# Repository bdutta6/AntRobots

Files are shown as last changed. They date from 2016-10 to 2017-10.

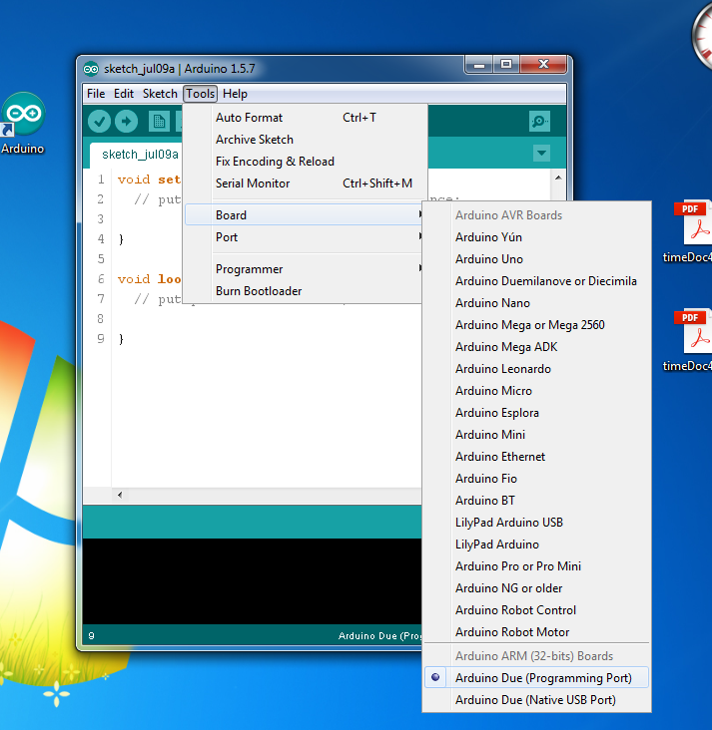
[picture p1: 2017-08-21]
docs/gettingStartedDoc/progPort.png

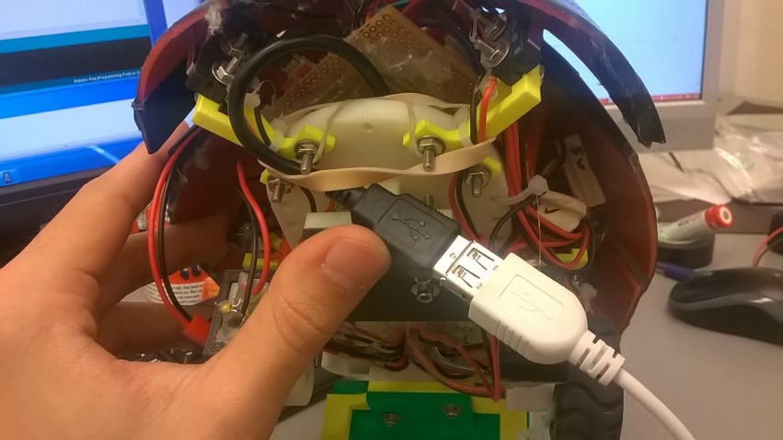
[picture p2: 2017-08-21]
docs/gettingStartedDoc/usbConnection.jpg

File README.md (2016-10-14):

# ant-robots

##Contributors

Initial Author: Vadim Linevich  
Email: vadim.linevich@gmail.com  

Modified by: Jungsoo Park  
Email : ryanryan0906@hotmail.com  

Modified by: Bahnisikha Dutta  
Email : bahnisikha3474@gmail.com  

Modified by: Ross Warkentin  
Email: ross.warkentin@gmail.com  

[Guide to .md files](https://guides.github.com/features/mastering-markdown/)

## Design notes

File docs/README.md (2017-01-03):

### September 27, 2016 
This serves as an e-introduction among all of us—Magnus and I are interested to see if his swarm work can be integrated with our ant robot work to learn if collisions among densely packed task oriented collectives of robots can be used to ensure good flow, etc. I suggest that all the students and postdocs cc’d on this email self-organize to trade info on what we (they) are doing and then in the coming weeks we can all meet to see if anything emerges...The new research direction on using ant-inspired collisions in swarm robot control/localization seems very interesting.

### October 4, 2016  
Grad Groups meeting today featured a woman from the library who overviewed the different resources available to graduate students. For research in engineering, she recommended compendex and inspec as good databases.

### October 5, 2016
I was supposed to have a Skype call with JSP today to review the robotic ant systems, but he was not able to get online. Instead, we chatted on the phone, and I took down the following notes:

* Mechanically it is sort of sorted out
  *	Two of them are not working well (Echo and Charlie?)
* When you connect the batteries, you need to separate the batteries completely off of the wires
* Issues are not commented within the code

I also spent a good amount of time today studying the codebase and learning its architecture. I think I have a good understanding of it, and I love the thorough documentation. I am not sure I understand the Watch Dog Timers (WTD), and I haven’t found a satisfactory explanation of them online. I would love an explanation of them from JSP.

### October 6, 2016  
I continued reviewing the code, and Dr. Goldman showed me how to turn on the robots. There is a black switch on the side which turns it on and off, as well as a button on the main board which can be used to reset the robot.
All of the batteries were dead, so there are two things that I need to do to get started:

1. Learn how to charge the batteries
2. Make a power cable so that the robots can run off of a power supply (3.6V).

### October 7, 2016

Will mentioned to me yesterday that the recharging process while the ants are running is not a straightforward process, and there are several files floating around on the lab desktop with tables I think might be necessary for regulating the charging method. See “C:\Users\vlinevich3\Desktop\Charging MPR121 Program vals.xlsx”.

Continued going through the documentation left by JSP and fleshing out the Robotic Ant Status to get a better feel for the architecture and pre-existing problems. I also started up a Trello Board to track proposed changes from JSP. The Trello board is populated with the “List of things that need to be done in the future” in the Ant Robot Mk.2 Software Documentation

Calling it a day. Feeling better about navigating the code. There seems to be some extraneous stuff left over from previous iterations, but I’d prefer to just get things running for now before going back and modifying working code to basically just look pretty. Best practices can be implemented after I have proven that I can get data with what we have right now.

I was hoping to hear from JSP today, but I might just shoot him an email with all of my documented questions later tonight.

[Guide to .md files](https://guides.github.com/features/mastering-markdown/)

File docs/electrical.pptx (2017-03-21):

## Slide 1

Bat 3.7-4.2V

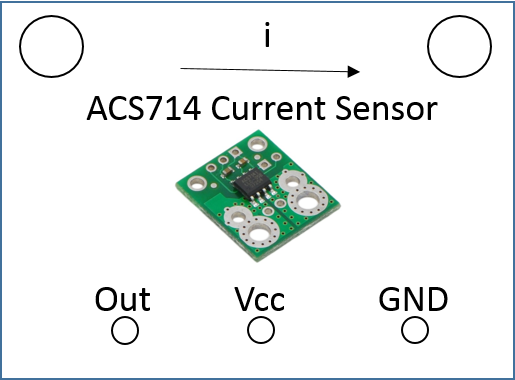
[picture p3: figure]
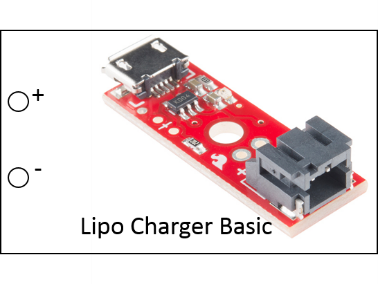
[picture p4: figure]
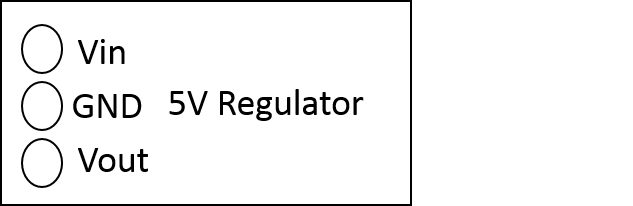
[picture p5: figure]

Due I/O Pin

Due Vin

Due 5V

Due Control Pin

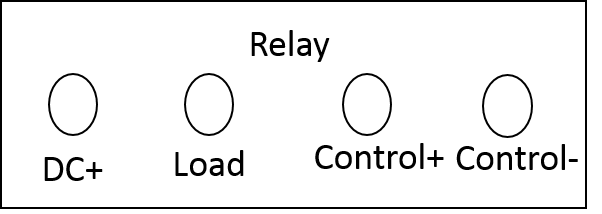
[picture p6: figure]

5V High current line

Batt GND

Due GND

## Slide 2

Vin

WW

GND

Vout

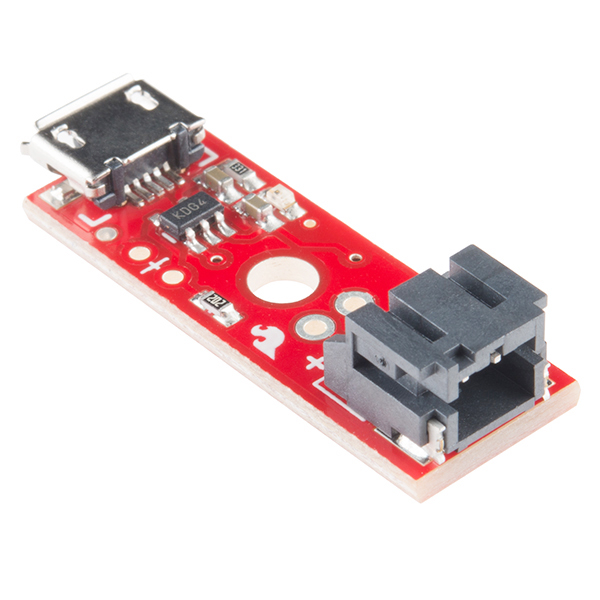
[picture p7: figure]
SparkFun LiPo Charger Basic - Micro-USB

Lipo Charger Basic

+

ACS714 Current Sensor

i

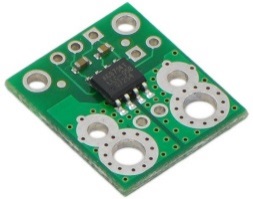
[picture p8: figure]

Out

Vcc

GND

Relay

DC+

Load

Control+

Control-

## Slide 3

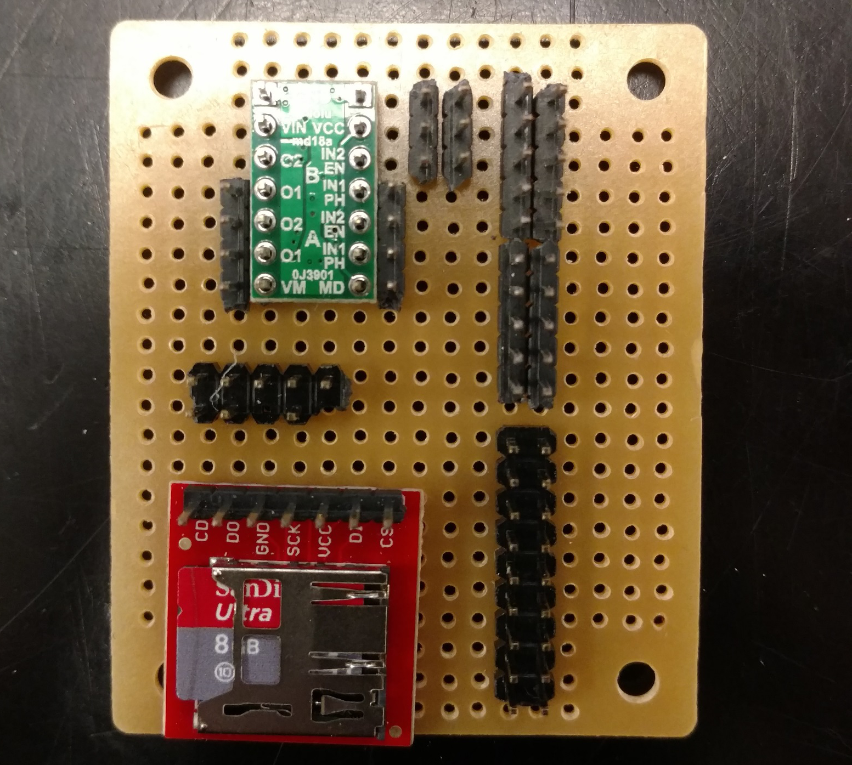
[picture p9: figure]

5V High Current

GND Due

GND

5V Due

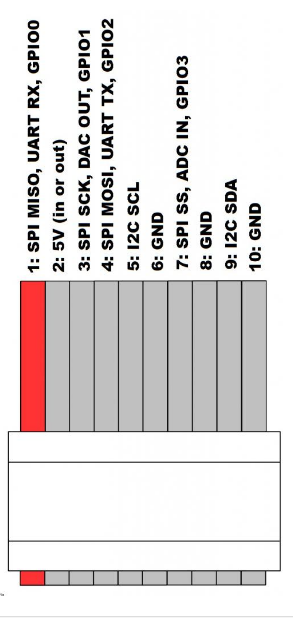
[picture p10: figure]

3.3V Due

Due Pin 4

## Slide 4

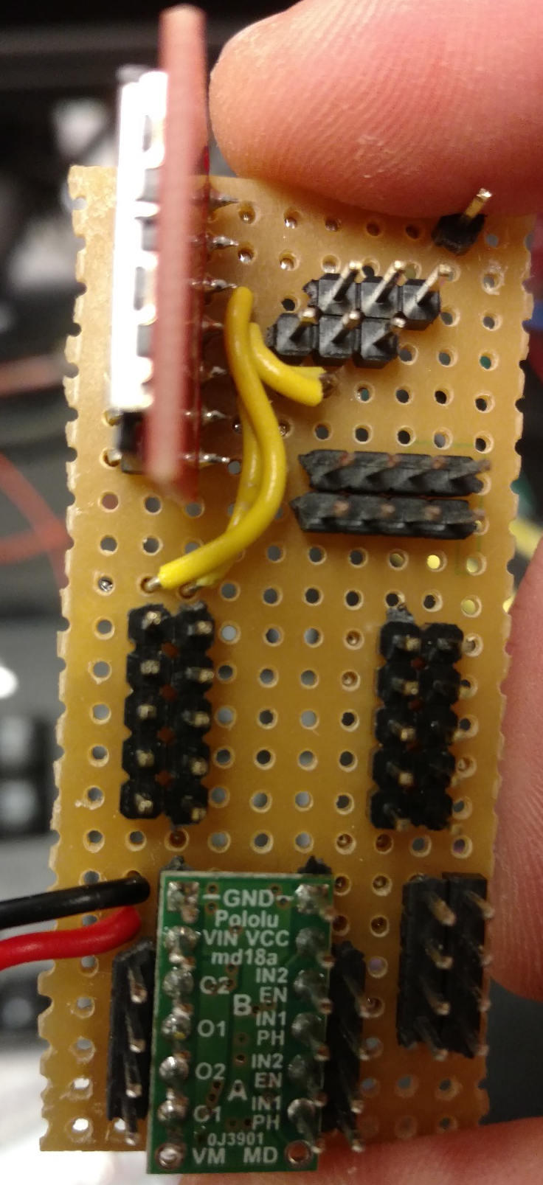
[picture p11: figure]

1 2
3 4
5 6
7 8
9 10

SPI Ribbon - Chip Reader:
1 – D0
3 – SCK
4 – D1

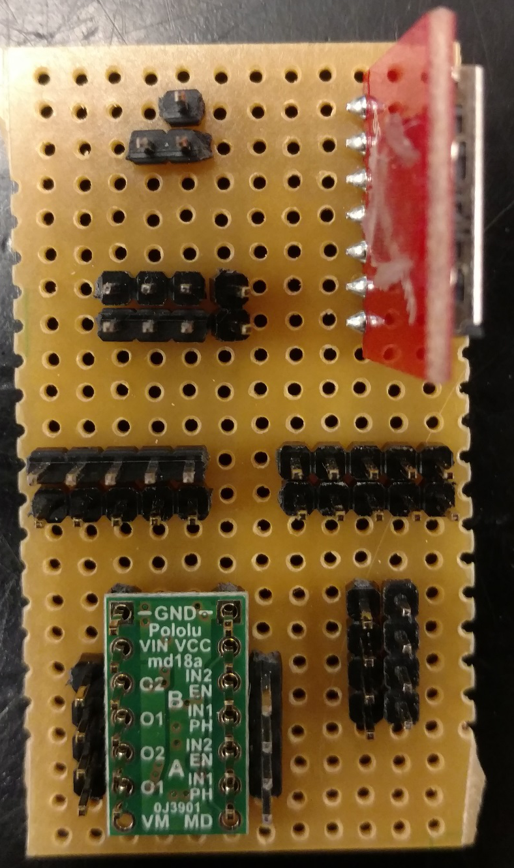
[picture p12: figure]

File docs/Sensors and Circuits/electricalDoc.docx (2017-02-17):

Due 5V – 800mA max

- Current sensor (draws 13mA at 5V)
- Hall effect sensors (9mA each x 4 sensors = 36mA total)
- Pixy (150mA at 5V)

Due 3.3V – 800 mA max

- Mag3110 is 0.9mA max with required voltage between 1.95 and 3.6V
- MPR121 is 29microA at 1.71 to 3.6V
- IMU is 350 microA

5V regulated power supply

- Gripper servo with 1.2A stall current
- Pitch servo with 1.2A stall current
- Motor board 1.25A stall current each = 2.5A total
- Due Vin

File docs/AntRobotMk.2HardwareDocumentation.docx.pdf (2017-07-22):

# Ant Robot Mk.2 Hardware Documentation

Jungsoo Park

CRAB Laboratory

Georgia Institute of Technology

626-720-3140

ryanryan0906@hotmail.com

Added Sensors/Systems

- Magnetometer: (https://www.sparkfun.com/products/12670)

The ant robot has one magnetometer sensor located in the front lower section of the robot, as shown in figure 1, to detect any magnetic cohesive material in the front. This sensor is used to inform when the robot has reached the digging site, and trigger the excavation behavior.

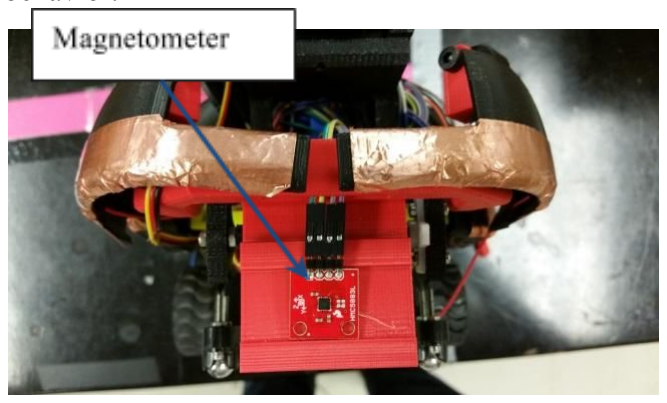
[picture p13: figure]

Figure 1: Magnetometer

- Gripper System:

The gripper system on the previous design featured a small gripper and servo, with an IR sensor to detect material in front, as shown in figure 2. In contrast, the new ant robot features more advanced gripper system, as shown in figure 3. It has much bigger gripper and stronger servo. In addition, it features more intelligent sensing capabilities, with the addition of Hall Effect sensors and force sensitive resistors. As a result, it is capable of excavating several times more material than that of the previous design. Furthermore, to ensure that the gripper system does not interfere with the robot’s capacitive sensors, it is designed to retract itself when it is not being used, but extend only when it is digging or depositing the material. Figure 3a shows the gripper in extended position, and figure 3b shows the gripper in retracted position. Figure 3c and figure 3d shows the griper in open position and closed position, respectively.

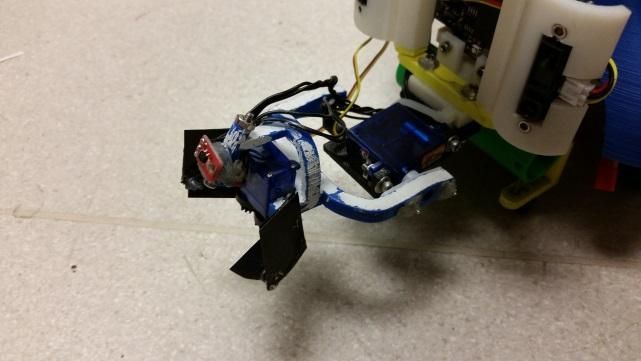
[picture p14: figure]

Figure 2: Gripper, Previous Design

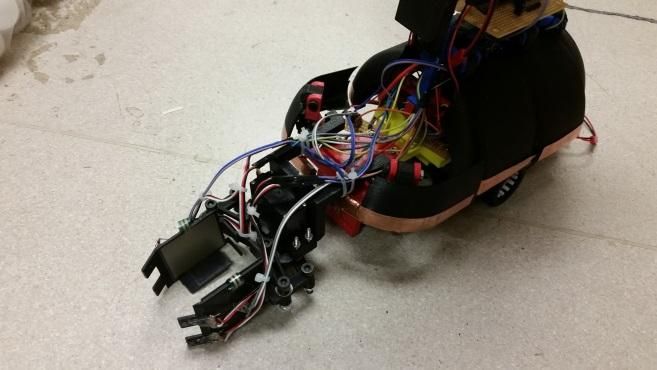
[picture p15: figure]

Figure 3a: Gripper, Extended Position

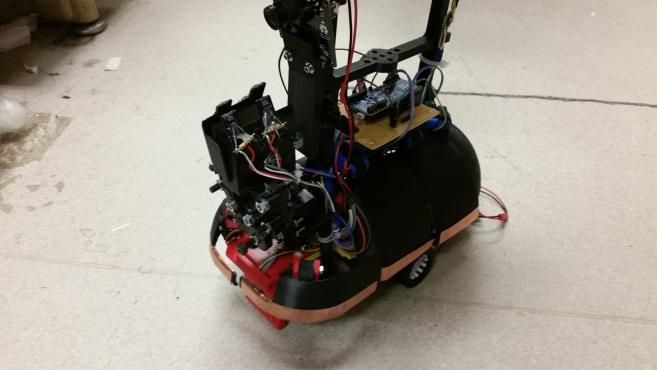
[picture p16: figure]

Figure 3b: Gripper, Retracted Position

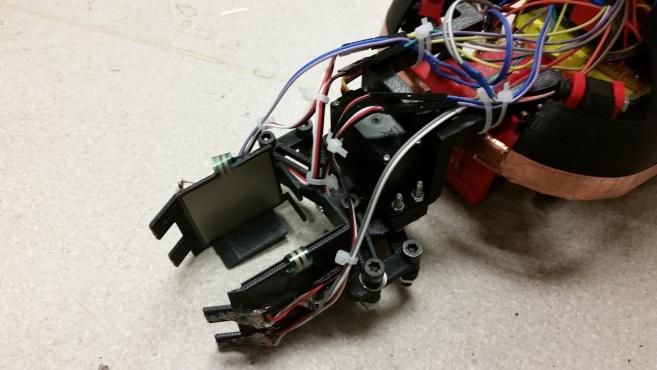
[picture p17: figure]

Figure 3c: Gripper, Open Position

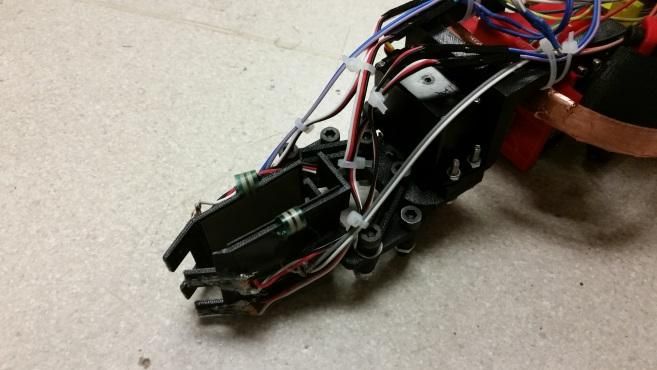
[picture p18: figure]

Figure 3d: Gripper, Closed Position

- Hall Effect Sensor:

Four Hall Effect sensors are located at the front tip of the gripper, as shown in figure 4. It is used as an alternative way to detect any magnetic cohesive material in front, as when the gripper is in extended position, it blocks the magnetometer and prevents it from detecting the magnetic cohesive material. In addition, these Hall Effect sensors can detect the accurate position of magnetic cohesive materials. This enables the robot to accurately position the gripper for optimal digging.

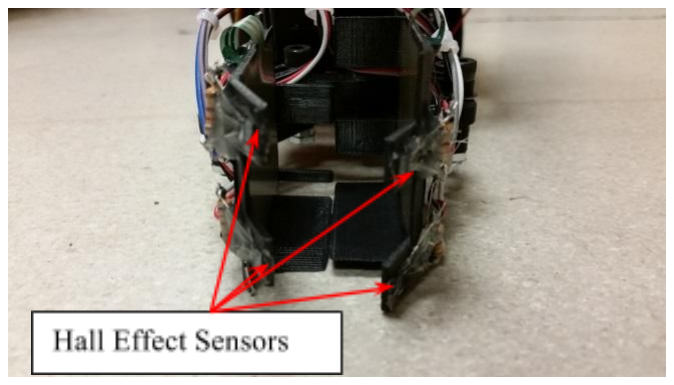
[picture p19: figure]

Figure 4: Hall Effect Sensors

- Capacitive Sensor:

The capacitive sensor is designed to detect and distinguish the tunnel wall and other ant robots. It is connected to eight copper foils surrounding the robot, as shown in figure 8. In addition, the tunnel walls have aluminum foils, as shown in figure 5. By monitoring the capacitance difference in the two different kinds of foils, it can distinguish the tunnel wall from other ant robots.

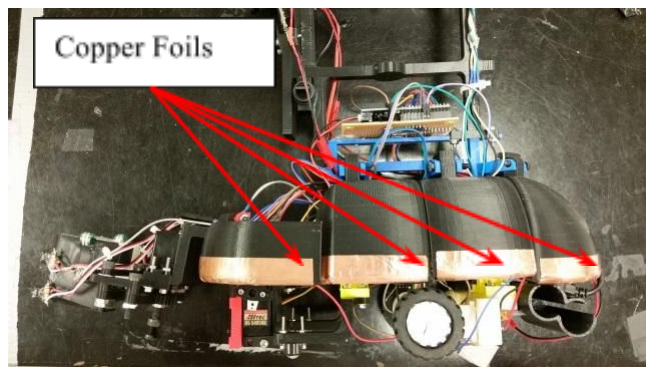
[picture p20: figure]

Figure 5: Capacitive Sensor

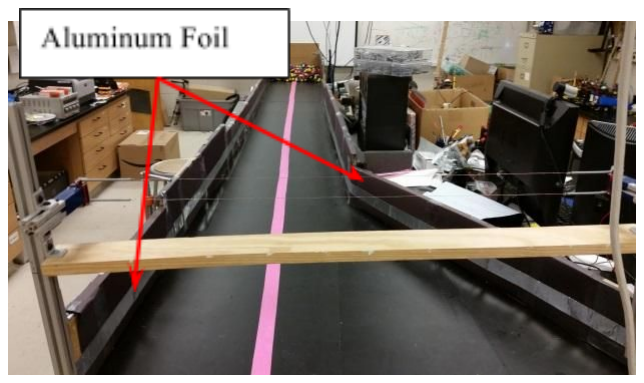
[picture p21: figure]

Figure 6: Tunnel

- Force Sensitive Resistor:

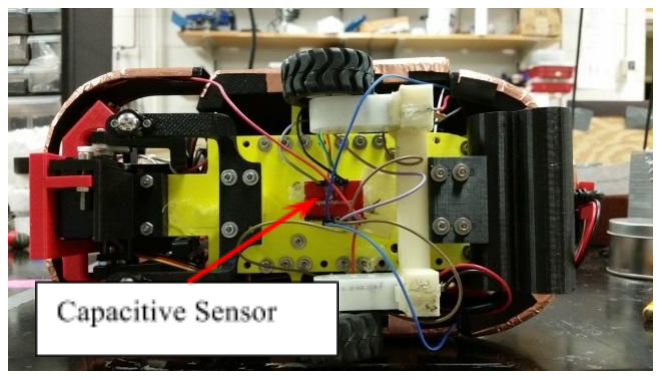
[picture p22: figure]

The force sensitive resistors are located inside the gripper to detect any material grasped by the gripper, as shown in figure 7. Depending on the pressure applied to the sensor pads, it gives different resistance, and by measuring the voltage difference, it can tell whether there’s any material inside the gripper.

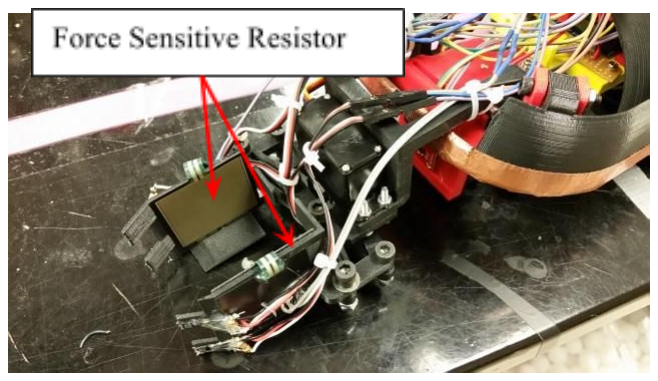
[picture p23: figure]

Figure 7: Force Sensitive Resistor

Arduino Fio Board Diagram

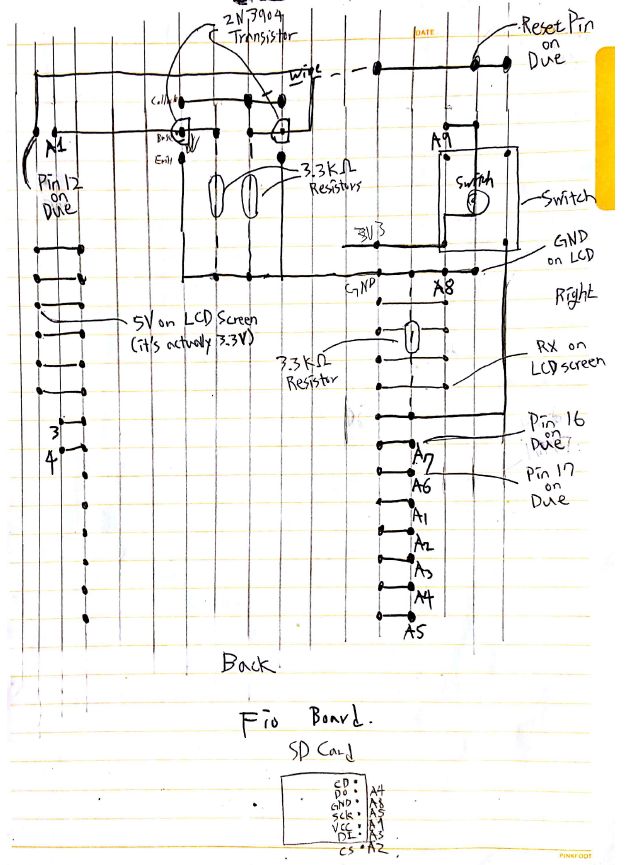
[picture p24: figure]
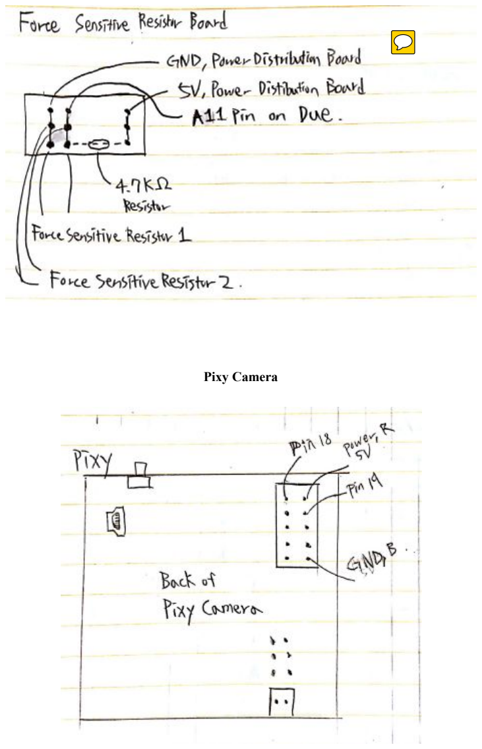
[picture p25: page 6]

Pixy Camera

Chraging Rod Board

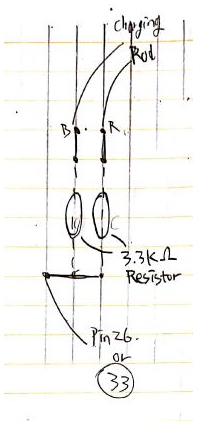
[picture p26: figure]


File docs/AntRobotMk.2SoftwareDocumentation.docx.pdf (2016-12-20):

# Ant Robot Mk.2 Software Documentation

Jungsoo Park

CRAB Laboratory

Georgia Institute of Technology

626-720-3140

ryanryan0906@hotmail.com

## List of things that need to be done in the future:

Improvement on capacitive sensor:

When the robot accelerates, it often stays tilted at an angle, since the back is heavier than the front. This often causes the ant robot unable to detect other ant robots, because the copper foil may not touch each other. Possible solutions are extending the copper foil upward to cover more surface (this should not affect capacitive sensor value much, but probably needs to be recalibrated) and lowering the front caster wheel by a few millimeters to shift center of weight forward.

Improvement on turning in/after turn_reversal mode:

The robot often does not complete turning in turn_reversal mode, and it often decides to turn again and again. It doesn’t seem like the turn_reversal mode is the cause, as it seems to turn after completing the turn_reversal mode. Rather, it is likely due to the PD controller not calibrated correctly, thus overshooting the pheromone trail by a lot, or Pixy camera not having enough field of vision.

Checking turn_reversal mode:

I already checked to see if turn_reversal mode works correctly in a normal run (i.e. the robot goes back and forth from digging), but it still needs to be checked in other runs, such as Lorentz run, when it decides to go back to charging due to low battery, or when it comes out of rest mode. Please check to see that this mode correctly puts the robot into the next mode correctly.

Robot Direction in Digging Mode:

The robot sometimes stays at a wrong angle when digging, thus failing to dig anything. This should be easy to correct; it probably needs TurnHeading function called right before digging attempt (maybe disable contact response, set preferGyro=false; and make sure that the robot doesn’t change its mode afterwards).

Cohesive material stuck inside robot gripper:

Sometimes the cohesive material stays stuck inside the robot, prompting the robot to attempt dumping mode repeatedly. Consider suppressing this behavior after certain number of trials. To do this, you need to look at both DumpingMode and GoingInMode. There is a function that triggers it to go back to dumping when it detects something inside its gripper. However, beware that this also enables the robot to immediately go back to dumping after a reset. Reset often happens after it successfully dug something, so I added this function to not lose progress after reset.)

Reset Problem:

After successful excavation, the robot often resets itself in exitTunnel mode. This problem was solved by adding a check function in GoingInMode. When it detects something inside its gripper in GoingInMode, it prompts the robot to immediately go back to dumping. This solution may conflict with the problem above. Note that this problem has no impact on robot’s functionality; it doesn’t reset memory, but only loses a few seconds while resetting.

Robot Echo Problem:

The robot Echo has issues with its two wheel motors. It accelerates to much faster speed compared to other robots, and this doesn’t seem like software issue. Consider replacing the whole wheel motor assembly. Make sure that the capacitor on the wheel motors are correct ones. Also make sure that the wiring is correct.

Robot Charlie Problem:

The robot has issues with its IMU sensor. The heading values from the IMU sensor seems to stick to wrong values. I already replaced the IMU several times, but it didn’t make any change. Consider replacing the wiring and the Arduino Due.

## Common Problems of the Robot and Solutions

Problem: Ant robot goes into digging mode even though there’s no cohesive material in front.

Solution: Magnetometer MAG3110 sensor is either damaged or not functioning. Check the sensor. The magnetometer is prone to physical damage as well, so consider replacing it with a new one.

Problem: The robot goes into turn_reversal mode even though there’s nothing inside its gripper.

Solution: Force sensitive resistor is either damaged or not functioning. Check the sensor.

Problem: The robot keeps resetting itself.

Solution: The voltage regulator may be overheating. Separate the battery power completely from the robot and let the voltage regulator cool down for a few minutes.

Problem: The robot doesn’t move at all or doesn’t track the pheromone trail.

Solution: The Pixy Camera may have lost focus or its color designation. Reprogram or refocus the camera accordingly. You can also check whether the camera is functioning properly by visually checking for its blinking light.

## Added Sensors/Systems

Hall Effect Sensors


Figure: Hall Effect Sensors

Please look at GripperSensor.cpp and GripperSensor.h for the code. There is no specific test function for these sensors, but you can use RUSensor.IsDetected() for testing (this tests the hall effect sensor located on Right Up). Change RU to LU, RD, or LD to test other hall effect sensors.

Magnetometer MAG3110


Figure: Magnetometer

Please look at MAG3110.cpp and MAG3110.h for the code. To test the sensor, search “for magnetometer MAG3110 sensor test and calibration” in the setup in the main code, and enable that section.

Capacitive Sensor MPR121


Figure: Capacitive Sensor


Figure: Tunnel

Please look at CapacitiveSensor.cpp, CapacitiveSensor.h, and mpr121.h for the code. To test this sensor, search to “for capacitive sensor test and calibration” in the setup in the main code, and enable that section. In addition, go to FioWirelessV4.ino file, and then enable “enable this part when calibrating/testing the capacitive sensor” section, and then disable “disable this part when calibrating/testing the capacitive sensor” section. This should display the capacitive sensor reading from one pin to the LCD screen.

Force Sensitive Resistor


Figure: Force Sensitive Resistor

Please look at CheckPayload() function in the main code. There is no dedicated function for testing this sensor, but CheckPayload() function can be used to test this sensor.

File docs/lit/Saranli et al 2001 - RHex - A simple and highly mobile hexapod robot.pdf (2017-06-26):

# RHex - A Simple and Highly Mobile Hexapod Robot

Uluc. Saranli∗, Martin Buehler† and Daniel E. Koditschek∗

∗Department of Electrical Engineering and Computer Science

The University of Michigan, Ann Arbor, MI 48109-2110, USA †Center for Intelligent Machines

McGill University, Montreal, QC H3A 2A7, Canada

Abstract

In this paper, we describe the design and control of RHex, a power autonomous, untethered, compliant-legged hexapod robot. RHex has only six actuators — one motor located at each hip — achieving mechanical simplicity that promotes reliable and robust operation in real-world tasks. Empirically stable and highly maneuverable locomotion arises from a very simple clock-driven, open-loop tripod gait. The legs rotate full circle, thereby preventing the common problem of toe stubbing in the protraction (swing) phase. An extensive suite of experimental results documents the robot’s significant ”intrinsic mobility” — the traversal of rugged, broken and obstacle ridden ground without any terrain sensing or actively controlled adaptation. RHex achieves fast and robust forward locomotion traveling at speeds up to one body length per second and traversing height variations well exceeding its body clearance.

I. Introduction


Fig. 1. The RHex experimental platform (ai.eecs.umich.edu/RHex).

In this paper we report on a power autonomous legged vehicle, RHex, Figure 1, that easily traverses terrain approaching the complexity and diversity of the natural land-

This work is supported in part by DARPA/ONR Grant N00014-98-1-0747

TABLE I

Summary of Published Performance Reports: Hexapedal

Robot

Name | L(m)b | M(kg)b | V(m/s)b | V/L
CW Robot II [11] | 0.5 | 1 | 0.083 | 0.16
Dante II [5] | 3 | 770 | 0.017 | 0.006
Atillaa [4] | 0.36 | 2.5 | 0.03 | 0.083
Genghisa [3] | 0.39 | 1.8 | 0.038 | 0.097
ASVa [29] | 5 | 3200 | 1.1 | 0.22
Boadicea [6] | 0.5 | 4.9 | 0.11 | 0.22
Sprawlita [12] | 0.17 | 0.27 | 0.42 | 2.5
RHexa | 0.53 | 7 | 0.55 | 1.04 a Power autonomous

b L: Body length, M: Robot mass, V: maximum speed

scape. Table I subtantiates in part our belief that this machine breaks the speed record to date for power autonomous legged robot locomotion over uneven terrain by a considerable margin¹. RHex travels at speeds approaching one body length per second over height variations exceeding its body clearance (see Extensions 1 and 2). Moreover, RHex does not make unrealistically high demands of its limited energy supply (two 12V sealed lead-acid batteries in series, rated at 2.2Ah): at the time of this writing (Spring 2000), RHex achieves sustained locomotion at maximum speed under power autonomous operation for more than fifteen minutes.
The robot’s design consists of a rigid body with six compliant legs, each possessing only one independently actuated revolute degree of freedom. The attachment points of the legs as well as the joint orientations are all fixed relative to the body. The use of spoked wheels (or even highly treaded wheels) is of course an old idea. Compa-

1Unfortunately, there is not enough performance detail documented in the published robotics literature to unconditionally establish this claim. To the best of our knowledge, the very few robots that have been demonstrated to negotiate uneven terrain at all, travel at speeds far less than those we report here.

rable morphologies such as rimless wheels [13] or single spoked wheels [22] have been previously proposed for mobile platforms. Some compliant legged designs have been proposed for toys [20], and some rigid rimless wheeled designs have actually been commercialized by the toy industry [26]. However, the major difference between a single leg and a wheel with more than two spokes arises from the far greater range of control over the ground reaction forces (GRF) that the former affords relative to the latter. Wheels afford control primarily over the horizontal component of the GRF (assuming flat ground) through friction, incurring an essentially uncontrolled concomittant vertical component. In contrast, a leg, by admitting selection over the angle of contact, yields a GRF whose direction as well as magnitude may be substantially controlled. As soon as multiple spokes are added, the inter-spoke angle restricts the range of contact angles, thereby diminishing control affordance. Our design preserves the possiblity of achieving full GRF range while adding the virtues of tuned compliance, heretofore associated only with wheels.


Fig. 2. Comparative views of locomotion in the rough: the cockroach Blaberus discoidalis (top photo, courtesyof R. J. Full [14]) runs at 3.7 bodylengths (∼24 cm) per second [15], whereas RHex (bottom photo) presentlyruns at onlyone bodylength (∼50 cm) per second over comparablyscaled broken terrain (see Extensions 3 and 4).

The closest extant robots, one significant source of inspiration for the RHex design, are the second author’s Scout class quadrupeds (www.cim.mcgill.ca/˜arlweb) [9, 10, 28] that also feature compliant legs, and reduce mechanical complexity by the restriction of one actuator per leg². The central difference with respect to this design is the possibility of recirculating — i.e., treating the singly actuated leg as a single spoked “rimless wheel”. A second key design influence whose careful consideration exceeds the scope of this paper arises from biomechanics. R.J. Full’s video of a Blaberus cockroach racing seemingly effortlessly over the rough surface illustrated in Figure 2, was shown at an interdisciplinary meeting [27] motivating and initiating the development of RHex. The present design may be seen as instantiating the notion of a “preflex” [8] — implemented here in the clock driven mechanically self stabilizing compliant sprawled posture mechanics that Full proposed³ [15]. The notion of a “clock driven” mechanism arises in our choice of an controller to derive appropriate advantage of RHex’s mechanical design. At the time of this writing, RHex operates by tracking (via local PD contol) at each hip joint a copy of the reference trajectory depicted in Figure 4 that enforces an alternating tripod gait in an otherwise open loop manner. The two tripods are driven in relative antiphase. The three legs of a tripod are driven simultaneously through a slow “retraction” phase, putatively corresponding to ground contact, followed by a fast “protraction” phase designed to recirculate the legs away from the the ground around the axle just in time to reach the next “retraction” phase, putatively as the opposing tripod begins its “protraction” by rotating away from ground contact. No design we are aware of has heretofore incorporated this combination of controller simplicity, leg compliance, limited actuation and overall morphology, and no previously implemented legged vehicle has achieved the performance we now report.
Table I (modeled on, but extended from [6]) summarizes performance data for previous hexapedal vehicles respecting which we are aware of documented performance, with citations to refereed publications. It would be of considerable interest to compare across a broader range of machines. Unfortunately, it is not straightforward to normalize against morphology. For example, “body lengths per second” is clearly not an appropriately normalized measure of bipedal speed. We look forward to the eventual adoption of appropriately general performance metrics for legged locomotion within the robotics research community. For the present, it seems most useful to compare the design of RHex with some of its more closely related forebears. One of the better documented, faster, power autonomous hexapods, the OSU adaptive suspension vehicle (ASV) was designed to operate in the statically stable regime. The deleterious consequences of design complexity have been observed in Dante II [5], a tethered hexapod whose exposure to severe environmental conditions have apparently been the most extreme of any robot yet documented in the

2Scout II travels at just under two bodylengths per second, but traverses only level ground.
3See [2] for a technical discussion of some aspects relating the bioinspiration behind this design to its performance.

archival literature. On a smaller scale, there have been many platforms inspired by insect locomotion [3, 4, 6], all designed for statically stable gaits. Their speeds were thus limited even though their design afforded greater kinematic freedom over limb motions. A notable exception in the smaller scale is Sprawlita [12], a tethered hexapod which can achieve a very impressive 2.5 body lengths per second locomotion speed as a result of its careful (compliant leg) design, and construction (offboard pneumatic actuation and small size).
For most of these machines, rough terrain performance and obstacle crossing capabilities are not carefully documented in the literature. There are only a few examples where such capabilities are reported in detail [5, 29], but even these are not suitable for assessing relative performance due to differences in scale and the lack of a consistent set of experiments and measures. Without more or less uniform standards of reporting, it becomes very difficult to test the claim that the relative speed (we use body lengths per second), relative endurance (we use specific resistance but also provide actual run-time data as well), relative mobility (we provide a metric characterization of the various terrain features) of one design is superior to another. Thus, beyond the specifics of design and performance, we believe that the paper makes a distinct contribution to the robotics literature by establishing new standards of rigor in empirical performance reporting for legged vehicles.
In summary, we believe this new design opens up a large range of new possibilities for control of locomotion, while still meeting the constraints imposed by contemporary actuation and energy storage technology on engineering autonomous robotic platforms. At the present time, we are unable to provide a mathematically informed analysis of how and why RHex performs over the range of reported behaviors. Instead, in this first archival paper, we present careful empirical documentation of a narrow but very useful behavioral suite — a base range of locomotion capabilities at relatively high speeds over relatively challenging terrain — and observe that no other power autonomous legged design has ever before been demonstrated to exhibit a comparable breadth of mobility behaviors.

II. Design and Modeling

A. Design Concept and Morphology

In all robotics applications, mechanical complexity is one of the major sources of failure and considerably increases the cost. Our design emphasizes mechanical simplicity and thereby promotes robustness. Autonomy, a critical component of our aspiration toward real-world tasks in unstructured environments outside the laboratory, imposes very strict design constraints on the hardware and software components. It is often impossible to achieve with simple modifications to a system otherwise designed for non-autonomous operation. These constraints also justify our preference for overall simplicity — in particular towards minimizing the amount of actuation and limited reliance on sensing.
Our design, depicted in Figure 3, consists of a rigid body with six compliant legs, each possessing only one independently actuated revolute degree of freedom. The attachment points of the legs as well as the joint orientations are all fixed relative to the body.


Fig. 3. The compliant hexapod design.

This configuration admits an alternating tripod gait for forward and backward locomotion, and possibly other more elaborate behaviors such as leaping, stair climbing etc. Moreover, the symmetry of this idealized model allows identical upside-down operation and imposes no restrictions on forward directionality. We explore some of this behavioral repertoire both in simulation and experimentally in Section IV and Section V, respectively.

B. The Compliant Hexapod Model

In this section, we present a dynamical model of the morphology described in the previous section. Prior to the construction of the experimental prototype, this model enabled us to assess the viability of the design through simulation studies. Augmented with the actuator model of Section IV-A, it proved to be an invaluable tool in the design process.
Two reference frames, B and W are defined in Figure 3, the former attached to the hexapod body and the latter an inertial frame where the dynamics are formulated. In B, we define the +y direction to be forward and the +x direction to be the the right side of the robot. The position and orientation of the rigid body are described by rb ∈ R³ and Rb ∈ SO(3), respectively, expressed in W. Table II details the notation used throughout the paper.
Each leg is assumed to be massless and has three degrees of freedom. The leg state is described in spherical coordinates [θi,φi,ρi]

T whose origin is at ai in the body frame⁴.

4Note that (rb, Rb), vi and fi are related through the coordinate transformation −Rb(ai + vi)= fi + rb

TABLE II

Notation

States
rb, Rb | body position and orientation
α | body yaw angle
Leg states and parameters
ai | leg attachment point in B
fi | toe position in W
vi | := [θi,φi,ρi] T leg state in spherical coordinates
vi | := [vxi ,vyi ,vzi ] T leg state in cartesian coordinates
legi | stance flag for leg i
Forces and Torques
Fri | radial leg spring force
τθi | bend torque in θi direction
τφi | hip torque in φi direction
Controller Parameters
tc | period of rotation for a single leg
ts | duration of slow leg swing
φs | leg sweep angle for slow leg swing
φo | leg angle offset
u | := [tc,ts,φs,φo] control vector
∆φo | differential change in φo for turning
∆ts | differential change in ts for turning.

B.1 Equations of Motion

Our formulation of the equations of motion for the hexapod model is based on individually incorporating the ground reaction forces at each leg. To this end, it will suffice to analyze a generic leg parametrized by its attachment and touchdown points, ai and fi, respectively. As a consequence of the assumption that the leg is massless, the rigid body experiences the ground reaction force on the leg, resulting in effective force and torque vectors acting on the center of mass. For each leg i =1, ..., 6, following projections on B, we have,

Fi =

- − cos θi sin φi | sin θi sin φi | − cos φi
sin θi | cos θi | 0
cos θi cos φi | − sin θi cos φi | − sin φi
| Fri
| τθi /ρi
| τφi /(ρi cos θi)

τi =(vi + ai) × Fi

which are the force and torque contributions of a single leg to the overall system dynamics, respectively. The cumulative effect of all the legs on the body is simply the sum of the individual contributions from the legs in contact with the ground, together with the gravitational force.

FT = 00 −mg T
+ Rb

6

i=1

legiFi | (1)
τT | = Rb

6

i=1

legiτi | (2)

(3)

The contact states of the legs are indicated by legi. In consequence, the dynamics of the hexapod are governed by the standard rigid body dynamics under external torque and force inputs [18]. Note also that, the discrete transitions in the contact states of the legs result in a hybrid dynamical system, whose behavior can be substantially different than that of its continuous constituents alone.

III. Control Strategy

The present prototype robot has no external sensors by which its body state may be estimated. Thus, in our simulations and experiments, we have used joint space closed loop (“proprioceptive”) but task space open loop control strategies. The algorithms that we describe in this section are tailored to demonstrate the intrinsic reliability of the compliant hexapod morphology and emphasize its ability to operate without a sensor-rich environment. Specifically, we present a four-parameter family of controllers, that yields translation and turning of the hexapod on flat terrain, without explicit enforcement of quasi-static stability. In Section V-C, we demonstrate the capabilities of this family of controllers on our experimental platform, over a wide range of terrain conditions, from flat terrain to a rough, broken surface.
All controllers generate periodic desired trajectories for each hip joint, which are then enforced by six local PD controllers (one for each individual hip actuator). In this respect, the present controller family represents one nearextreme along the spectrum of possible control strategies, ranging from purely feedforward (i.e., taking no notice of body state), to purely feedback (i.e., producing torque solely in reaction to leg and rigid body state). It seems likely that neither one of these extremes is best and a combination should be adopted. The simulations and experiments presented in this paper attempt to characterize the properties associated with the sensorless feedforward extreme, which, when RHex has been endowed with sensors, we hope to complement with feedback to explore the aforementioned range.
An alternating tripod pattern governs both the translation and turning controllers, whereby the legs forming the left and right tripods are synchronized with each other and are 180o out of phase with the opposite tripod, as shown in Figure 4.

left tripod right tripod

Fig. 4. The motion profiles for left and right tripods.

A. The Forward Alternating Tripod Gait

The open loop controller’s target trajectories for each tripod are periodic functions of time, parametrized by four variables: tc, ts, φs and φo. In a single cycle, both tripods go through slow and fast swing phases, covering φs and 2π − φs of the complete rotation, respectively. The period of both profiles is tc. In conjunction with ts, it determines the duty factor of each tripod, with respect to the duration of their slow and fast phases. The time of “double support” td (where all six legs are in their slow phases, but possibly not all of them touching the ground) is hence determined by the duty factors of both tripods. Finally, the φo parameter offsets the motion profile with respect to the vertical (see Figure 4). Note that both profiles are illustrated to be monotonically increasing in time; but they can be negated to obtain backward locomotion.
Control of locomotion is achieved by modifying these parameters for a particular desired behavior during locomotion. In Section IV, our simulation studies reveal correlations of these parameters with certain behavioral attributes.
B. Turning

We have developed two different controllers for two qualitatively different turning modes: turning in place and turning during translation. These controllers are inspired by differential turning in wheeled and tracked vehicles, where opposite perturbations to contralateral actuators result in a net rotation of the body on the plane. Analytical understanding of this behavior in the context of our design awaits careful mathematical treatment of RHex’s dynamics as well as accurate models of ground contact.
The controller for turning in place employs the same leg profiles as for forward locomotion except that contralateral sets of legs rotate in opposite directions. This results in the hexapod turning in place in the direction determined by the rotational polarity of the left and right sets of legs. Note that the tripods are still synchronized internally, maintaining three supporting legs on the ground. Similar to the control of the forward locomotion speed, the rate of turning depends on the choice of the particular motion parameters, mainly tc and φs.
In contrast, we achieve turning during forward locomotion by introducing differential perturbations to the forward running controller parameters for contralateral legs. In this scheme, tc is still constrained to be identical for all legs, which admits differentials in the remaining profile parameters, φo and ts, while φs remains unchanged. Two new gain parameters, ∆ts and ∆φo are introduced. Turning right (towards +x in the coordinate system of Figure 3, defining +y as forward) is achieved by using ul =[tc,ts + ∆ts,φs,φo +∆φo] and ur =[tc,ts − ∆ts,φs,φo − ∆φo] for the legs on the left and right sides, respectively.

IV. Simulation Studies

Our simulation studies in this section use the dynamical model described in Section II-B, together with an actuator model to demonstrate the feasibility of basic locomotion behaviors of our design under practical actuation limitations. The presented results provide a proof of concept for the design, justifying the building of our prototype and the extensive experiments of later sections. In order to limit the scope of the paper to an appropriate length, however, we have excluded impact of these models and the resulting simulation tools in refining the kinematic and dynamical parameters of our experimental prototype.

A. Actuator Model

The model of Section II-B does not impose any constraints on the choice of the hip torques τφi . In practice, however, torque limitations are one of the major challenges in the design of autonomous legged vehicles, even for statically stable modes of operation. In order to capture this aspect of our design space in the subsequent simulation studies, we incorporate a simple model of the hip actuation.

Shaft speed (rev/min); Shaft torque (mNm)

Fig. 5. Torque characteristics for the Maxon RE118751 20W DC motor, reproduced from the manufacturer’s datasheet. The shaded band illustrates the range of torque deliverable bythe motor.

Figure 5 portrays the experimentally measured torquespeed characteristics for the DC motors used in our experimental platform. The shaded band captures the range of torque deliverable by the motor at any particular speed⁵. Our simulations incorporate this model by saturating hip torque command outputs of the local PD controllers as a function of the leg angular velocity.

B. Simulation Environment

All the simulation results of the next section are produced by SimSect, a simulation environment that we have created primarily for the study of the compliant hexapod platform [31]. SimSect can efficiently and accurately deal with the hybrid nature of the model resulting from discrete ground contact model, preserving the relatively simple dynamics of the continuous model.
The hexapod simulation with SimSect uses the same dimensions and body mass as our experimental platform (see Section V). However, some of the dynamical parameters used in the simulations, including the leg spring and damping constants, and the ground friction coefficient are not experimentally verified and are likely to be different from their actual values. Nevertheless, the relatively accurate match between the simulations and the experimental platform regarding their morphology and mass parameters still admit qualitative comparisons of behavior.
C. Simulation Results

In this section, we verify in simulation that the controllers of Section III are able to produce fast autonomous forward locomotion of the hexapod platform.

s (rad); 1.2 _ ⁽rad=s⁾

(a)

(b)

Fig. 6. (a) Average forward velocity y˙ as a function of tc and φs over 5s of operation, during which the robot always settled down to an approximatelyperiodic trajectory. Remaining controller parameters are chosen as ts = tc/2, φo =0. (b) Average inplace turning yaw rate α˙ as a function of tc and φs over 5s of operation.

Figure 6 shows the the forward velocity (a) and the turning yaw rate (b) as functions of controller parameters tc and φs. Although the remaining parameters ts and φo have

5Note that the we have conservatively approximated the DC motor characteristics by assuming constant maximum torque for second and fourth quadrants.

considerable effect on both the body oscillations during locomotion as well as the forward velocity, through manual tuning, we identified certain values for them to yield good performance in most cases. As a consequence, throughout these simulations, φo is kept constant and ts is chosen to be half the stance time. Nevertheless, it is clear that proper tuning of all four controller parameters is necessary to achieve the smoothest and fastest locomotion performance. The effects of a hand tuned, intuitively “best” choice for a given tc and φs is demonstrated in Figure 7 and the associated Extension 5, a typical forward translation with an average velocity of 0.55m/s .


Fig. 7. Forward bodyvelocityfor a simulation run with tc =0.5s, φs =0.7rad, ts =0.3s and φo =0.03rad.

These results suggest the opportunities for considerably improved performance resulting from the introduction of feedback to regulate the forward locomotion and turning yaw rate of the compliant hexapod platform. We sketch our approach to these future opportunities in the conclusion.

V. Experimental Platform
A. Hardware Description

We have built an experimental platform (Figure 1) as an instantiation of the design concepts of Section II-A. RHex is an autonomous hexapod robot with compliant legs, very close to the model described in Section II-B. All the computational and motor control hardware is on board, together with two Panasonic 12V 2.2Ah sealed lead-acid batteries for power autonomous operation. A PC104 stack with a 100 MHz Intel 486 microprocessor, together with several I/O boards performs all the necessary computation and implements the controllers of Section III. A remote control unit provides the user input for giving higher level commands such as the forward speed, and turning direction, presently via a joystick.
Each leg is directly actuated by a Maxon RE118751 20W brushed DC motor combined with a Maxon 114473 twostage 33:1 planetary gear [24], delivering an intermittent stall torque of 6 Nm. The motor angle, and thus the leg angles, are controlled via 1 kHz software PD control loops. The control software also features several safety measures, including fault detection for the encoders, estimation of the rotor temperatures to avoid motor damage, and a watchdog timer which disables the motors and resets the computer in case of software failures.
The main body measures 53x20x15 cm, and roughly matches the symmetries of the ideal model, except for the slightly lower center of mass and the larger length of the bottom side. The legs are made from 1 cm diameter Delrin rods and are “C” shaped to increase compliance in the radial direction and permit easy clamping to the gear shaft (see Extension 6). The leg length is 17.5 cm, measured as the vertical distance from ground to the gear shaft when standing up. We experimentally measured their compliance to be approximately 4500 N/m in their expected operating region. The encoder/motor/gear stacks protrude from the main body and the maximum widths of the front and back legs amount to 39.4 cm, measured at half the leg length. To provide clearance for the rotating front and back legs, the motors for the middle legs are further offset and result in a maximum width of 52 cm. The total mass of the robot is 7 kg with each leg contributing only approximately 10 g.
B. Visual Measurement Apparatus

Absent any inertial sensing on RHex, we devised a simple visual tracking system to record the robot’s position and orientation in the sagittal (obstacle crossing experiments) and the horizontal (turning and rough surface experiment) planes. Four Light Emitting Diodes (LEDs) were attached to the robot’s body and a set of stationary calibration LEDs were placed close to the extremes of the camera’s field of view. The experiments were then conducted in complete darkness, which provided for very high contrast recordings of the LED markers. Thanks to this greatly simplified visual data, standard computer vision algorithms were then employed to extract the planar robot position and orientation up to a 1% accuracy in the average velocity computations.

C. Experimental Results

In the sequel, we will document the robot’s speed over various terrains, its maneuverability, obstacle crossing capability, and payload. Furthermore, energy efficiency and runtime are critical performance criteria for any untethered robot. Thus the energetic performance of the robot is carefully documented, but it must be noted that at the time of this writing, no efforts have been made to optimize it. All experiments — except the random obstacles experiment, Figure 12, Section B-D — were run untethered and we document the average power consumption, based on recordings of the battery voltage and current.
To measure energy efficiency we use the “Specific Resistance” [17], ε = P/(mgv), based on the robot’s weight, mg, and its average power consumption, P, at a particular speed, v. Specific resistance was originally used to compare the energy efficiency of animals of vastly different sizes,

TABLE III

Experimental statistics carpet | | linoleum | grass | gravel
total # of runs | 10 | 11 | 16 | 25 | 32 | 14 | 14 | 26
successful runs | 10 | 10 | 10 | 10 | 16 | 10 | 10 | 10
electronics & hardware problems | - | - | 1 | 5 | 6 | - | - | 2
deviation from course | - | 1 | - | 5 | 7 | - | - | 5
operator mistake a | - | - | 5 | 5 | - | 3 | 2 | 2
stuck on obstacle | - | - | - | - | 3 | 1 | 2 | 7

rough

single obst.

comp. const.
obst. course

aThese failure modes include steering in unwanted directions, failure to trigger the timing switch and the power cord wrapping around the legs.

where the average power measured the rate of metabolic energy expenditure, based on oxygen consumption. The same measure has been used to compare the energy efficiency of a range of different robots [1, 19, 21, 35]. Unfortunately, attention to energy efficiency and its reporting is fairly rare in robotics, and not consistent. For example, the power, if documented at all, is given as the mechanical power delivered by the actuators, the peak mechanical power of the main power source, or the total electrical power consumption. Therefore, quantitative energetic comparisons of past robots are not always precise. For electrically actuated mobile robots like RHex it makes most sense to report the total electrical power consumption (which includes the power for sensing and computing), since it will determine, together with the battery capacity, the all important runtime. In any case, the battery power consumed will always provide an upper bound on joint power, or mechanical power as the battery is the only source of energy in the system. Throughout the experiments, the control parameters were set to fixed values, and these were only modified by the operator via the joystick commands in an attempt to steer the robot along a straight line. The speed command input was used solely for starting and stopping the robot. Experimental findings are summarized in Table III and Figures 9-8, and discussed in Sections V-C.1 through V-C.6. A detailed account of the setup, measurement protocols and failure modes is presented in the Appendix.

C.1 Forward Locomotion

This first set of experiments documents RHex’s maximum velocity, power and specific resistance with the twostroke open loop controller of Section III while traversing carpet (see Extension 7 for an example run), Linoleum, grass and coarse gravel. The robot moved well over these indoor and outdoor surfaces, with only minor velocity variations between 0.45 m/s and 0.55 m/s as shown in Figure
8. The velocity on Linoleum was lowest due to intermittent slipping, which also causes a larger standard deviation of the runs compared to carpet. In the current prototype, the relatively high natural frequency of the system and the open loop nature of the leg trajectories limit the maximum speed due to out of phase vertical body oscillations, which reduce traction. The surface irregularities of the outdoor grass and gravel surfaces provided improved traction, and therefore average velocities slightly above 0.5 m/s, but also resulted in larger variations between the runs. The specific resistance (power consumption) was lowest on carpet with 2.21 (80 W) and highest on gravel with 3.74 (140 W). We experimented with control parameter settings to reach the maximum robot velocity on office carpet and linoleum, and selected u = [0.45, 0.2, 51, 0]. The grass and gravel surfaces were not tested with these settings prior to the reported experiments. Figure 8shows the average velocity, power consumption and the specific resistance over ten runs, with standard deviations for all the experiments. All the experimental data as well as the associated analysis scripts can also be found in Extension 8. Table III summarizes the failure modes and statistics for all the experiments described

in this Section.; carpet; linoleum; grass; gravel; rough; obst. course; payload; Average forward velocity (m/s); Average power consumption (W); Average specific resistance; C.2 Turning; ongoing research.; C.3 Obstacle Crossing; _ (rad=s); The obstacle crossing capa- bilities of the simple open loop walking controller were eval- uated with two different ob- stacles - a 15 cm high Sty- rofoam block and a compos- ite obstacle with a maximum height of 22 cm, as shown in Figures 10 and 11, respectively (also see Extensions 10 and; The robot was able to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

Fig. 8. Comparison of average forward velocityand energetics for different experiments (also see Extension 8).

As our simulation study had predicted, steering is possible, even though the leg actuation is limited to motion in the sagittal plane only, via differential motion between left and right legs. We selected control parameters which

TABLE IV

Controller parameters for turning at different speeds

x˙ (m/s) | tc (s) | ts (s) | φs (rad) | φo (rad) | ∆φo (rad) | ∆ts (s)
0 | 1.0 | 0.6 | 35 | 0.0 | 0.0 | 0.0
0.16 | 1.2 | 0.7 | 25 | 0.0 | 6.0 | −0.02
0.28 | 0.8 | 0.45 | 35 | 0.0 | 7.5 | 0.0
0.39 | 0.53 | 0.33 | 40 | 0.0 | 6.5 | 0.0

resulted in turns in place and robot speeds up to about 0.4 m/s (see Table IV) on most flat surfaces including carpet, linoleum, grass and gravel. The maximum forward velocity is reduced during turning, because the differential leg motion precipitates the onset of the speed limiting vertical body oscillations. The maximum yaw angular velocities increase almost linearly with forward velocity up to 0.19 rad/s at 0.39 m/s, as illustrated in Figure 9. Interestingly, the resulting turn radius is almost constant with approximately 2 m. Turning in place provides the highest yaw angular velocity of 0.7 rad/s, although it is not possible to directly compare its performance to differential turning, which is a qualitatively different controller. At present, we do not understand completely the relationship between the controller parameters and effective yaw rates, a subject of

Fig. 9.; Turning yaw rate; as a function of forward; velocity.; See Extension; as the robot climbs over the ob- stacle, and increases again af- terwards. Since the robot’s tra-

9 for all the data and
analysis scripts associated with the turning experiments.

jectory over the obstacle depends greatly on how the legs
engage it, the standard deviation of the average velocities increases over the obstacle. The average speeds varied most (largest standard deviation) after the composite obstacle, since it depended much on how the robot landed. As a further illustration of the robot’s motion, the forward velocity from a particular run, and the robot’s body in the sagittal plane at 0.5 s intervals during the same run are shown as well.
0 | 0.5 | 1 | 1.5 | 2

0

0.2

0.4

0.6

0.8

1

1.2

0 | 0.5 | 1 | 1.5 | 2

0

0.2

0.4

˙y (m/s)

y (m)

z (m)

Fig. 10. Sagittal plane data during simple obstacle crossing. The data in the top portion of the graph shows forward velocityaverages and standard deviations before, during and after the obstacle, averaged over ten runs. The solid line is one particular run. The bottom half shows a projection of the robot’s bodyonto the sagittal plane in 0.5 s intervals (horizontal and vertical axes at the same scale). See Extension 12 for all the experimental data and the analysis scripts.

C.4 Obstacle Course

To demonstrate RHex’s rough terrain capabilities, we constructed the obstacle course depicted in Figure 12. It consisted of ten randomly spaced obstacles of 12.2 cm height (that is, 60% of the leg length and exceeding ground clearance by 1.8cm). This was by far the most challenging of the experiments, requiring the largest number of runs before ten successful completions. Most failures can be attributed to the open loop nature of the walking controller, which had to climb blindly over ten randomly spaced obstacles, sometimes as little as half a body width apart, but all higher than the ground clearance. This had to be done successfully over a distance of 8.13 m, avoiding all the failure modes detailed in the Appendix. Yet, for the ten successful runs, RHex was able to maintain an average velocity of 0.36 m/s over the length of the obstacle course (Figure 8). The best run finished in only 17.78 s, or an average velocity of 0.46 m/s, with a specific resistance of 8.17. The punishing nature of this course is reflected in the power

−0.5 | 0 | 0.5 | 1 | 1.5 | 2

0

0.2

0.4

0.6

0.8

1

1.2

−0.5 | 0 | 0.5 | 1 | 1.5 | 2

0

0.2

0.4

˙y (m/s)

y (m)

z (m)

Fig. 11. Sagittal plane data during composite obstacle crossing. The data in the top portion of the graph shows forward velocityaverages and standard deviations before, during and after the obstacle, averaged over ten runs. The solid line is one particular run. The bottom half shows a projection of the robot’s bodyonto the sagittal plane in 0.5 s intervals (horizontal and vertical axes at the same scale). See Extension 13 for all the experimental data and the analysis scripts.

consumption of more than three times that of walking on carpet, over five times the specific resistance, and a high rate of component breakdown: During the obstacle course experiments, RHex broke three legs, burned several circuit traces, and fractured its frame.

0 | 1 | 2 | 3 | 4 | 5 | 6 | 7 | 8
| | | | y (m)

Fig. 12. Scale drawing of RHex and the obstacle course.

C.5 Rough Surface

This last rough terrain experiment is an attempt to evaluate RHex’s performance in a similar environment to that negotiated by the Blaberus cockroach in [15]. Our efforts at re-creating such a surface at RHex’s scale can be evaluated visually in Figure 2 as well as Extensions 3 and 4. To our surprise, RHex was able to traverse this surface with random height variations of up to 20.32 cm (116% leg length, Figure 13) with relative ease at an average velocity of 0.42 m/s (Figure 8). RHex’s planar trajectories during the two fastest and the two slowest successful runs are shown in Figure 14. In addition, body state associated with an example run can be found in the multimedia appendix Item 11.


Fig. 13. Sample profiles of row 6 (columns 8,9 and 10) with RHex staticallyposed for comparison.

Average velocity: 0.56 m/s; Start; Finish; Average velocity: 0.52 m/s; Average velocity: 0.27 m/s; Average velocity: 0.34 m/s

Fig. 14. The two fastest (top) and the two slowest (bottom) robot trajectories in the horizontal plane as RHex moves over the rough surface. The plots also show projections of the bodyonto the horizontal plane in 1 s intervals. See Extension 14 for all the experimental data and the asociated analysis scripts.

C.6 Payload and runtime

To demonstrate RHex’s payload capacity, we mounted an additional mass of 7.94 kg (one 10 lb and one 7.5 lb weight-lifting barbell) to the bottom of RHex’s body and adjusted the control parameters for lower speed and a small sweep angle (c6 =0.7, 0.2, 14, 0). The robot was able to transport this additional mass, more than its own total mass, at about half its maximum speed (0.25 m/s) with a specific resistance of about 3. These averages were obtained from ten runs. This payload is close to the limit of the current design, and may not be practical, since the motors are not powerful enough to raise the robot when lying on the floor even when all six legs are used. A careful analysis of tradeoffs between payload and speed in legged systems operating in a quasi-static regime is provided in [23], but is not directly applicable to RHex.
Finally, the endurance of RHex was tested in standby mode, with the motors enabled, and maintaining a standing position, and while walking at maximum speed on carpet. The average standby runtime was 48minutes, and 18 minutes for continuous walking (both values averaged over 5 successive experiments).

VI. Conclusion

Nimble, robust locomotion over general terrain remains the sole province of animals, notwithstanding our functional prototype, RHex, nor the generally increased recent interest in legged robots. RHex, endowed with only a rudimentary controller, uses what might be termed the engineering equivalent of “preflexes” [8, 15] to negotiate relatively badly broken terrain at relatively high speeds — performance beyond that heretofore reported for autonomous legged vehicles in the archival literature. We are convinced that further systematic application of certain operational principles exhibited by animals will achieve significant increases in RHex performance, and inform the evolution of the underlying mechanical design of future prototypes as well. To conclude the paper, we provide a brief sketch of these principles and how they may be applied.

Accumulating evidence in the biomechanics literature suggests that agile locomotion is organized in nature by recourse to a controlled bouncing gait wherein the “payload”, the mass center, behaves mechanically as though it were riding on a pogo stick [7]. While Raibert’s running machines were literally embodied pogo sticks [30], more utilitarian robotic devices such as RHex must actively anchor such templates within their alien morphology if the animals’ capabilities are ever to be successfully engineered [16]. We have previously shown how to anchor a pogo stick template in the more related morphology of a four degree of freedom monopod [32]. The extension of this technique to the far more distant hexapod morphology surely begins with the adoption of an alternating tripod gait, but its exact details remain an open question, and the “minimalist” RHex design (only six actuators for a six degree of freedom payload!) will likely entail additional compromises in its implementation. Moreover, the only well understood pogo stick is the Spring Loaded Inverted Pendulum [34], a two degree of freedom sagittal plane template that ignores body attitude and all lateral degrees of freedom. Recent evidence of a horizontal pogo stick in sprawled posture animal running [25] and subsequent analysis of a proposed lateral leg spring template to represent it [33] advance the prospects for developing a spatial pogo stick template in the near future. Much more effort remains before a functionally biomimetic six degree of freedom “payload” controller is available, but we believe that the present understanding of the sagittal plane can already be used to significantly increase RHex’s forward speed, and, as well, to endow our present prototype with an aerial phase.

Appendix

I. Index to multi-media Extensions

TABLE V

Index to multi-media extensions

Ext. | Media type | Description
1 | Video | RHex traversing simple outdoor obstacles
2 | Video | Demonstration of RHex’s leg compliance
3 | Video | Example simulation with Sim-Sect
4 | Video | Basic walking gait
5 | Video | RHex traversing a single high sty-rofoam obstacle
6 | Data | Data and analysis scripts for the single obstacle experiments
7 | Video | RHex traversing a composite ob-stacle
8 | Data | Data and analysis scripts for the composite obstacle experiments
9 | Video | Front view of RHex over the rough surface obstacle
10 | Video | Top view of RHex over the rough surface obstacle
11 | Data | Data and analysis scripts for the rough surface experiments
12 | Video | RHex traversing a challenging in-door obstacle
13 | Data | Data and analysis scripts for turning experiments
14 | Data | Power, speed and specific resis-tance data and analysis scripts for all the experiments.

The multi-media extensions to this article (see Table
V) can be found online by following the hyperlinks from

www.ijrr.org.

II. Details of the Experimental Setup and

Failure Modes

A. Forward Locomotion

We ran the robot over carpet, linoleum, grass and gravel. The carpet and linoleum surfaces were standard office floors found close to the lab. The grass was wet on the day of the experiment and showed height variations of about 2 cm. The gravel patch contained fairly large gravel pieces (see Figure 1) between three and eight cm diameter. For all the experiments, the robot was driven over a test stretch of 2 m. In order to obtain precise timing and to synchronize the data logging with the test stretch, a switch was mounted in the front of the robot, which was triggered as the robot ran into a Styrofoam panel held at the beginning and the end of the test stretch. The runs over each surface were repeated until ten successful runs were obtained. The average velocity and power consumption for each run was then computed with the available data.
Ten successive experiments were run for the carpet surfaces with no failures. One run on the Linoleum floor was discarded, since the robot deviated too much from the straight line. A total of 16 runs on grass were necessary, with six runs discarded. In five runs, the operator failed to align the start or stop trigger panel properly, and the front legs pushed it aside, preventing the switch to be actuated. One run was abandoned due to R/C noise in the remote control command input. Gravel was more challenging - of the 25 runs, five were discarded because the robot deviated too much from a straight line, five due to the operator missing the trigger switch, one due to remote control noise, and four because the front switch broke on impact with the trigger panel.
B. Turning

The turning experiments were run on carpet. In order to reduce the data processing for this set of experiments, only six runs were processed in this fashion for each forward velocity, instead of the usual ten. Only few runs were discarded due to noise in the remote control which interfered with the velocity and/or the steering command.

C. Obstacle Crossing

The first obstacle was a 1.22 m long strip of 3” (7.62cm) thick Styrofoam board, a standard insulating construction material, cut to 15 cm height. This represents 80% of the robot’s leg length and exceeds it’s 10.5 cm ground clearance by 4.6 cm, or almost 50%. The Styrofoam was chosen for this experiment and the random obstacle course described below for its ready availability, low cost, and ease of cutting. It is softer than wood, yet hard enough that the robot does not deform it. The second obstacle was built from construction lumber and consisted of a 10 cm high and 63 cm wide base (as viewn in the sagittal plane) on top of which a 8.5 cm high and 3.5 cm wide block was mounted at a distance of 25 cm from the front and a 12.5 cm high and 8.5 cm wide second block was mounted at a distance of 50 cm from the front. In both experiments the control parameters were the same as in the walking experiments above. All data shown was obtained by the visual tracking procedure described in Section V-B, with the camera oriented for a perpendicular view of the sagittal plane. The average forward velocity of each run was obtained before, over, and after the obstacle.
Fourteen successive experiments were required and logged for both obstacles. From the runs over the first obstacle, the robot failed to surmount it only once, but the vision post processing algorithm failed to extract reliable position data for three successful runs, when the robot’s direction after obstacles deviated significantly from straight path. From the fourteen successive runs over the composite obstacle, the robot failed twice to surmount the obstacle, and the vision post processing failed to extract data from the post-obstacle portion of two runs.
D. Obstacle Course

The experimental setup for the obstacle course consisted of ten randomly spaced obstacles of 12.2 cm height. The free spaces between the ten 3” (7.62cm) wide Styrofoam blocks were 1.07, 0.47, 0.78, 0.68, 1.02, 0.91, 0.66, 0.29 and 0.96 m, selected between 0.5 and 2 body lengths from a uniform random distribution. Thus the total obstacle course extended over 8.13 m, which also includes one half body length before and after the course. The time between start and finish was measured via a stopwatch. During these experiments an operator attempted to keep the robot on course using the limited directional control described above. Nevertheless, the directional disturbances due to the obstacles caused the robot at times to veer towards the lateral limits of the 1.2 m wide course. In those instances, operators who followed the robot along the course, placed a Styrofoam panel along the lateral limits to make up for the lack of side walls. When the collision angle with these walls was sufficiently small, the robot re-aligned itself with the course.
Due to the large number of runs required for this experiment, and the high power requirements, we made an exception and ran the robot from higher capacity external batteries via an umbilicus. This greatly reduced the experimental effort by eliminating the need to recharge and exchange the on-board batteries. However, no performance improvement resulted from this arrangement, compared to running off freshly charged on-board batteries. The on-board batteries were kept in place to maintain the total robot mass.
A total of 26 successive experiments on the obstacle course were recorded. Of these, 16 were discarded for the following reasons: The robot turned itself sideways beyond quick recovery (2), shut itself off (1), required operator intervention through the R/C unit, such as turning in place or short reversal of direction to complete the course (3), turned itself on its back either by climbing up against the side walls (1) or the obstacle (3), wrapped the power cord around the legs (1), ends up “sitting” aligned with and on top of an obstacle, unable to reach the ground (3), or burned electrical circuits (1). The remaining eleven runs were used to calculate the velocity, power and specific resistance data shown in Figure 8.
E. Rough Surface

In order to re-create Full’s rough surface [15], we compared the height distribution of his environment [14] to checkerboard arrays of randomly uniformly distributed block heights. When scaled to RHex’s dimensions, we de-

1 | 2 | 3 | 4 | 5 | 6 | 7 | 8 | 9 | 10 | 11 | 12

1

2

3

4

5

6

12" | | 8" | | 4" | | 7" | 11" | 12" | 9" | | 6" | 6" | | 7" | 7" | 8"
9" | | 8" | 10" | | | 9" | 6" | 10" | 8" | | 5" | 4" | | 7" | 5" | 6"
5" | 11" | | 10" | | 10" | | 10" | 12" | 5" | 11" | | 8" | 10" | | 6" | 8"
9" | 4" | 11" | | 8" | 8" | 10" | 11" | | 5" | 12" | 6" | 9" | 12"
10" | 6" | 12" | 10" | | 9" | 11" | | 8" | 8" | 9" | 6" | 5" | | 8"
4" | 9" | 7" | 8" | 10" | 8" | 5" | 6" | 9" | 12" | 9" | 11"

Start

Finish

Fig. 15. Height distribution over the rough surface

cided that a height variation of between 4” (10.16 cm) and 12” (30.48cm), or 1.16 leg lengths was a good match (Figure 15). To simplify cutting by a local lumber yard, the block heights were discretized to 1” (2.54 cm) increments. The block width of 7” (17.78cm) permitted the use of four standard 3.5”x3.5” (8.89cm x 8.89 cm) cross section lumber per checkerboard block. The total surface consisted of 72 blocks (6 by 12) thus requiring 288 individually cut lumber sections. The robot was run in the direction of the 12 block length of the surface, with wall panels on each side. Its cartesian position and orientation, projected onto the horizontal plane, was measured with the visual tracking setup described in the steering experiment, above.
We carried out 32 experiments on this surface, with a success rate of 50%. During the unsuccessful runs, the robot either ran head-on into a side wall or into one of the isolated posts (typically the isolated high block with coordinates 2,9 in Figure 15 (3), broke a leg (twice), hit one of the walls (3), had to back up and continue forward (4). Also, four of the experiments did not complete due of R/C failure. From the 16 experiments that were successfully recorded, we have used 10 with the cleanest vision data to facilitate the post-processing.

Acknowledgements

This work was supported in part by DARPA/ONR Grant N00014-98-1-0747. Bob Full consulted on many of the design decisions and provided numerous tutorial explanations of the biomechanics literature. Greg Sharp built the software for the processing of our vision data. Jim Berry helped in setting up and running many of the experiments. Noah Cowan offered very helpful advice concerning modeling and simulation. Liana Mitrea made invaluable contributions in the mechanical construction of the hexapod platform.

References

[1] M. Ahmadi and M. Buehler, “The ARL Monopod II Running Robot: Control and Energetics,” in IEEE Int. Conf. Robotics and Automation, Detroit, MI, May 1999, pp. 1689–1694.
[2] R. Altendorfer, U. Saranli, H. Komsuoglu, D. E. Koditschek, Jr. H. B. Brown, M. Buehler, N. Moore, D. McMordie, and R Full, “Evidence for spring loaded inverted pendulum running in a hexapod robot,” in International Symposium on Experimental Robotics, Hawaii, 2000.
[3] C. Angle, “Genghis: A six-legged autonomous walking robot 1989, SB thesis.
[4] C. Angle, “Design of an artificial creature,” M.S. thesis, Massachusetts Institute of Technology, Cambridge, MA, 1991.
[5] J. E. Bares and D. S. Wettergreen, “Dante II: Technical Description, results and lessons Learned,” International Journal of Robotics Research, vol. 18, no. 7, pp. 1–29, July 1999.
[6] M. Binnard, “Design of a small pneumatic walking robot,” M.S. thesis, Massachusetts Institute of Technology, Cambridge, MA, 1995.
[7] R. Blickhan and R. J. Full, “Similarity in multilegged locomotion: Bouncing like a monopode.,” Journal of Comparative Physiology, vol. A. 173, pp. 509–517, 1993.
[8] I. E. Brown and G. E. Loeb, “A reductionist approach to creating and using neuromusculoskeletal models,” in Biomechanics and Neural Control of Movement. Springer-Verlag, In press.
[9] M. Buehler, R. Battagila, A. Cocosco, G. Hawker, J. Sarkis, and
K. Yamazaki, “SCOUT: A simple quadraped that walks, climbs and runs,” in Proceedings of the IEEE International Conference On Robotics and Automation, Leuven, Belgium, May 1998, pp. 1707–1712.
[10] M. Buehler, A. Cocosco, K. Yamazaki, and R. Battaglia, “Stable open loop walking in quadruped robots with stick legs,” in Proceedings of the IEEE International Conference On Robotics and Automation, Detroit, Michigan, May 1999.
[11] H. J. Chiel, R. D. Beer, R. D. Quinn, and K. S. Espenchied, “Robustness of a distributed neural network controller for locomotion in a hexapod robot,” IEEE Transactions on Robotics and Automation, vol. 6, no. 3, pp. 293–303, 1992.
[12] J. E. Clark, J. G. Cham, S. A. Bailey, E. M. Froehlich, P. K. Nahata, R. J. Full, and M. R. Cutkosky, “Biomimetic Design and Fabrication of a Hexapedal Running Robot,” in Proceedings of the IEEE International Conference On Robotics and Automation, Seoul, Korea, May 2001.
[13] Michael J. Coleman, Anindya Chatterjee, and Andy Ruina, “Motions of a rimless spoked wheel: a simple three-dimensional system with impacts.,” Dynamics and Stability of Systems., vol. 12, no. 3, pp. 139–159, 1997.
[14] R. J. Full. Personal communication.
[15] R. J. Full, K. Autumn, J. I. Chung, and A. Ahn, “Rapid negotiation of rough terrain by the death-head cockroach,” American Zoologist, vol. 38, pp. 81A, 1998.
[16] R. J. Full and D. E. Koditschek, “Templates and Anchors: Neuromechanical Hypotheses of Legged Locomotion on Land,” Journal of Experimental Biology, vol. 202, pp. 3325–3332, 1999.
[17] G. Gabrielli and T. H. von Karman, “What price speed?,” Mechanical Engineering, vol. 72, no. 10, pp. 775–781, 1950.
[18] H. Goldstein, Classical Mechnanics, Addison-Wesley, 1980.
[19] P. Gregorio, M. Ahmadi, and M. Buehler, “Design, control and energetics of an electrically actuated legged robot,” IEEE Trans. Systems, Man, and Cybernetics, vol. 27, no. 4, pp. 626–634, Aug 1997.
[20] H. G. Grimm Animated Toy, US Patent 2,827,735; 1958.
[21] S. Hirose, “A study of design and control of a quadruped walking machine.,” International Journal of Robotics Research, vol. 3, no. 2, pp. 113–133, 1984.
[22] E. R. Honeywell Walking Tractor, US Patent 1,375,752; 1920.
[23] M. Z. Huang and K. J. Waldron, “Relationship between payload and speed in legged locomotion systems,” IEEE Transactions on Robotics and Automation, vol. 6, no. 5, pp. 570–577, October 1990.
[24] Interelectric AG, Sachseln, Switzerland, Maxon Motor Catalog, 1997/98, www.maxon.com.
[25] T. M. Kubow and R. J. Full, “The role of the mechanical system in control: A hypothesis of self-stabilization in hexapedal runners,” Phil. Trans. R. Soc. Lond., vol. B. 354, pp. 849–862, 1999.
[26] Mattel’s | Major | Matt | Mason’s | #6304 | Space | Crawler
http://www.wildtoys.com/MMMPage/MattelPlaysets/mmm3part1.html.
[27] NSF Institute for Mathematics and Its Applications Spring 1998 Workshop on Animal Locomotion and Robotics. June 1-5 1998, http://www.ima.umn.edu/dynsys/spring/dynsys10.html.
[28] D. Papadopoulos and M. Buehler, “Stable running in a quadruped robot with compliant legs,” in Proceedings of the IEEE International Conference On Robotics and Automation, San Francisco, CA, April 2000.
[29] D. R. Pugh, E. A. Ribble, V. J. Vohnout, T. E. Bihari, T. M. Walliser, M. R. Patterson, and K. J. Waldron, “Technical description of the adaptive suspension vehicle,” International Journal of Robotics Research, vol. 9, no. 2, pp. 24–42, April 1990.
[30] M. H. Raibert, Legged robots that balance, MIT Press, Cambridge MA, 1986.
[31] U. Saranli, SimSect Programmer’s Manual, The University of Michigan, 1999, In preparation.
[32] U. Saranli, W. J. Schwind, and D. E. Koditschek, “Toward the Control of a Multi-Jointed, Monoped Runner,” in Proceedings of the IEEE International Conference On Robotics and Automation, Leuven, Belgium, May 1998, vol. 3, pp. 2676–82.
[33] J. Schmitt and P. Holmes, “Mechanical models for insect locomotion I: Dynamics and stability in the horizontal plane.,” Biological Cybernetics, vol. submitted, 1999.
[34] W. J. Schwind and D. E. Koditschek, “Approximating the stance map of a 2-dof monoped runner,” Journal of Nonlinear Science, vol. 10, pp. 533–568, 2000.
[35] K. J. Waldron and V. J. Vohnout, “Configuration design of the Adaptive Suspension Vehicle.,” International Journal of Robotics Research, vol. 3, no. 2, pp. 37–48, 1984.

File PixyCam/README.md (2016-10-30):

# PixyCam Firmware-y Things

The PixyCam is the hardware for the vision system on the ant robots. There is a well documented, and unresolved issue where the communication between the Due and Pixy hang in getBlocks(). The current solution is to restart the Due, which is why you will find the WDT calls sprinkled through the .ino file of the Due code. According to Vadim, the bricking issue is more frequent in the more recent versions of the firmware, though further testing should be conducted, due to the recent firmware updates.

### Uploading Firmware

As of 10/28/2016, all of the released version of the firmware are saved in this directory. At the moment, a working robot is using version 2.0.17 with roboJSP.prm. Information and methods regarding how to upload new (or perhaps old) firmware to the Pixy can be found [here](http://cmucam.org/projects/cmucam5/wiki/Uploading_New_Firmware).

### PixyCam Parameters

A number of .prm files were discovered on the lab machine, all of which were saved to this directory. I have uploaded roboJSP.prm to a robot, which runs well. I think it is important to note that the parameters, such as "Data out port" is set to a value that according to the online documentation should not work. Perhaps some undocumented changes have been made in the PixyCam software.

Information about communicating with the Pixy can be found [here](http://cmucam.org/projects/cmucam5/wiki/Porting_Guide).

Information about the Pixy serial protocol can be found [here](http://cmucam.org/projects/cmucam5/wiki/Pixy_Serial_Protocol).

Information about the Pixy/Arduino hookup can be found [here](http://cmucam.org/projects/cmucam5/wiki/Hooking_up_Pixy_to_a_Microcontroller_like_an_Arduino). Note that, as of 10/27/2016, the communication line used is UART. This method does not use handshaking, and is likely the issue for the bricking issue that WDT handles.

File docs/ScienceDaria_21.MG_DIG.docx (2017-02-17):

Idle active matter: excavation by confined and crowded task-oriented collectives

D. Monaenkova¹*, J. Aguilar²*, V. Linevich², B. Dutta¹, W. Savoie¹, M. A. D. Goodisman³, D. I. Goldman¹*.

¹ School of Physics, Georgia Institute of Technology, Atlanta, GA, USA

²School of Mechanical Engineering, Georgia Institute of Technology, Atlanta, GA, USA

³School of Biological Sciences, Georgia Institute of Technology, Atlanta, GA, USA

*Correspondence to: daniel.goldman@physics.gatech.edu

†Additional author notes should be indicated with symbols (for example, for current addresses).

Abstract (100-150): Ensembles of self-propelling elements, like colloidal surfers, active liquid crystals, bacterial biofilms, social insects, and robot swarms can spontaneously form clusters, clogs and jams. In many “task-oriented” collectives, avoiding formation of such structures is paramount for task completion, for example, during subterranean nest formation by social insects. Through the study of tunnel excavation by fire ants, autonomous robots, and cellular automata models, we demonstrate the importance of appropriate social behaviors in facilitating collective excavation in crowded, confined conditions. In particular, tools from the study of glass formation reveal how congestion, jams and even arrest due to high-density traffic can be mitigated via global social behaviors (a distribution of idleness) and local interactions (selective retreats). A particular combination of the above strategies emerges from optimization algorithms, (and is utilized by the ants), achieving effective and efficient excavation without the need for sophisticated sensing, planning and global control of the collective.

One Sentence Summary (150): Experiments and simulations of social insects and robots reveal how workforce heterogeneity governs the successful organization of confined collectives.

Active materials – ensembles of self-propelling elements – generically form patterns and structures (1, 2) in a diversity of artificial (3) and living systems: from colloidal surfers (3) to organismal collectives (4). In many biological systems (e.g. fish schools (5) or bird flocks (6)), such large scale ordering has beneficial biological functions (7, 8). For example, schooling behavior in fish is associated with defense against predators and foraging success, while clusters of bacteria exhibit quorum-sensing, promoting migration or the development of new growth modes.

However, structure formation in active matter systems can also have deleterious consequences, particularly in confined systems like pedestrian/vehicular traffic jams (9), competing bacteria biofilms (10), high density cell migration (11), jammed herds (12), ROBOTS CITE MATARIC and confined systems where flow rate is vital for proper colony function. In these situations, cluster formation may lead to clogging, preventing task completion or leading to substantial failure of the system.

MAKE ABOUT ROBOT WORK: We studied how clogs can be mitigated or managed in “task oriented” active matter—systems composed of elements which must work together to perform a task without central coordination. For example, clogs can form in biological systems like soil excavating ants and robot teams (13-16) which work in crowded, confined environments (Fig. 1). Some of the best examples come from ant and robot studies. While robotic swarms (16) have demonstrated how interactions with confining boundaries can produce organized collective motion, the challenges of extreme confinement are exemplified by our previous (17) and current (Fig. 1C, Fig. 4, supplementary materials) experiments with autonomous devices, which reveal how large groups of congested robots that excavate pellets in narrow tunnels without central command or social behaviors (defined as cooperation strategies among individuals) underperform single excavators due to traffic jams. XX MAKE SURE TO DISCUSS TASK ALLOCATION VS INTERFERENCE (FROM ROBOT LIT) But our work is different because we find and set up a distribution of labor pattern BLAH

Fire ant colonies (S. invicta) rapidly excavate and build elaborate nests (Fig. 1A) (18), despite being subjected to collisions among individuals and the confined spaces therein. We hypothesize that insect societies, which comprise 30% of global biomass (19), engage in social behaviors which minimize clogging. For example, we recently discovered that fire ants moving bi-directionally through a confined tunnel minimize their interaction times to maintain smooth traffic flow (20). We studied nest excavation of S. invicta to understand the social behaviors that improve performance either through reactive mechanisms that adapt to traffic or proactive measures that avoid traffic disruptions (Fig. 1B).

Ant experiments: Small groups (~30) of S. invicta workers were placed in transparent containers of wetted glass particles (Fig. 2A) with a soil moisture content of 1 or 10 percent of total particle weight (3 trials each). Ants excavated for 48 hours (with a single ant entering the tunnel as much as 426 times) along the container wall and used a variety of techniques to collect grains, form a pellet, and ascend the tunnel for deposition (21). A camera mounted to a motorized linear stage tracked the tunnel face as it was excavated (Fig. 2A, supplementary materials). We distinguished individual ant activity by marking ant abdomens with different colors (Fig. 1B). We logged the presence and behavior of each worker that entered the tunnel when they were in view of the camera (Fig. 2C). Ants exhibited a variety of social behaviors, from workload inequality (i.e. idleness) to a likelihood of giving up and retreating the tunnel without pellets (reversals), which seemed to be associated with successful collective excavation.

Idleness was characterized by workload inequality in the population, whereby a significant portion of ants (27 ± 17%) never entered the tunnel to excavate during the 48-hour period of observation. Lorenz curves (Fig. 2D) illustrate workload inequality by linking the cumulative share of workers in the population (ranging from the least to the most active individuals) to the cumulative share of activity by the group, whereby an ant is defined as active while present in the tunnel. The Gini coefficient (22) indicates the deviation of the workload from either perfectly shared (G = 0, all workers work equally) to completely unequal (G = 1, a single worker performs all work). Regardless of soil moisture, Lorenz curves were approximated by power law relationships (Fig. S2) with an average G = 0.7 ± 0.1.

Workload inequality has been observed in other social animals during foraging (22), whereby activity levels are not necessarily related to worker roles or specialization (22) and may change depending on the colony needs (23). We divided experiments into 12-hour “epochs” and found that the activity level of individual ants changed over time (Fig. S3), but the collective workload inequality remained consistent (Fig. S1). The Gini coefficient was affected neither by the soil moisture content (one-way chi-square, χ2 = 0.005, p = 0.95), the epoch of the experiment nor the colony (2-way ANOVA, F11, 24 = 0.3, p = 0.72 and p = 0.99)). Furthermore, when the most active excavators were removed from the group, other workers increased their activity and compensated for the loss, preserving the shape of the Lorenz curve (Fig. 2D inset, supplementary materials). Thus, given the consistency of the workload distribution, we hypothesize that idleness may play an adaptive role in modulating the crowded conditions of confined tunnels.

We also observed ant reversals during excavation, whereby an ant descended the tunnel but then retreated without excavating a pellet. Such behaviors were often associated with local crowding (Fig. 2E) at the excavation face (16.2 ± 11.9% of observations in 1% soil moisture and 9.7 ± 2.2% of observations in 10% soil moisture). Reversal behavior in crowded conditions occurs on foraging trails (24), and similar phenomena have been observed in swarming bacteria (10). The frequency of this seemingly unproductive behavior increased with increasing overall activity of ants (Fig. S4). We posit that such behavior serves as a feedback mechanism for controlling congestion during excavation.

Ant simulations: To examine the effect of experimentally observed social behaviors on large groups of excavating agents, we developed a cellular automata (CA) excavation model (Fig. 3A, supplementary materials), useful in elucidating the dynamics of ant tunnel traffic (20). The CA model consisted of a tunnel lattice with a width of two cells occupied by soil, empty space, an ascending ant, or a descending ant (Fig. 3A). Simulated ants could walk, excavate, deposit a pellet, or rest. We implemented reversals and unequal workload distributions on populations of 2 to 100 ants. Reversal behavior was implemented by a simple scheme, which designated a probability to abandon digging when an ant’s path to the excavation site was blocked by traffic for more than a pre-defined duration. While direct control of output workload distributions was not implemented, we modulated workload inequality by setting individual probabilities to return to the excavation site after pellet deposition (work probability).

The work probability distribution was determined with a genetic algorithm (GA) (Fig. 3B) on a 30-ant CA model, changing the work probability distribution to optimize excavation rate with each generation (supplementary materials). Regardless of the initial population, the simulation converged to an unequal workload distribution within a few generations (Fig. 3C). Notably, this theoretically optimized distribution resembled the experimentally observed workload distributions (Fig. 2D, green), suggesting that an unequal workload distribution is a robust mechanism and biological adaptation for improving excavation rate.

We found that populations greater than 3 ants resulted in irresolvable clogs, regardless of the workload distribution, unless ants were capable of reversal behaviors. Thus, we simulated both equal (Active ants) and GA work probability distributions (Lorenz ants) with an identical probability to reverse. Reversal probability, along with other simulation parameters, were selected such that 30 Lorenz ants produced experimentally observed ant digging rates (Fig. 2B).

Even with reversal behaviors, active ants performed poorly for populations of greater than 5 ants, whereas Lorenz ants were able to maintain relatively high excavation rates with large populations (Fig. 3D). Such a phenomenon, whereby the system performs worse when the individual system components attempt to maximize their own performance, is common for various multi-particle systems including vehicle and pedestrian traffic (25). Consequently, CA ant traffic resembles characteristics of vehicle traffic flow (26), whereby the mean flow rate ( q , defined as the rate of successfully depositing ants over time) of excavators in the tunnel is maximal at an intermediate tunnel density ( ρ , ratio of average number of ants in the tunnel to tunnel size) (Fig. 3E). This trend in q v ρ (the fundamental diagram) has been attributed to the transition between laminar flow and propagating traffic jams as density increases (27). Thus, we attribute the increased flow rate in higher populations of Lorenz ants to a reduction in overall tunnel densities afforded by an unequal workload distribution, thereby reducing the frequency of traffic jams for large ant populations. Not only do reversals and unequal workloads improve excavation rate, but a selective pressure for digging efficacy may robustly lead to an embedded idleness in populations of underground excavators.

Robotic Experiments: While CA simulations provide some insight into how various social behaviors affect excavation efficacy; simple simulation interactions cannot easily account for how real world complexities such as friction, particle geometry, maneuverability, and the nonexistence of traffic lanes affect system dynamics. Thus, we developed a system of excavating robots (Fig. S10) inspired by traversal strategies of ants to undertake “physical simulations” (Fig. 4A-D) in order to explore collective behavior during excavation. Rather than using centralized control, intelligent planning or communication, ants navigate confined spaces with local cues like head-on contact and pheromone feedback (24). Similarly, the robots “diggybots” FOR PRESS followed simple movement instructions triggered by onboard sensory feedback of the surrounding environment (supplementary materials). For example, rather than using collision avoidance schemes (14), the robots detected collisions with push switches on their outer shell, which triggered reactive clog resolution and navigation strategies such as steering away and reversing. Further, we constructed the tunnel to have a width of 3 robot widths (or 1.5 robot lengths), emulating the challenge of turning around in confined spaces. XXHYPOTHESIS: LAZY ANTS AND LAZY ROBOTS ARE LAZY BY DESIGN, NOT BY LOCAL INTERACTIONS…COMMENT ON MATARIC STRATEGIES

The effects of reversals and idleness on robot performance were examined individually with three behavioral strategies tested on groups of two to four robots. The first strategy (Active, Fig. S7) designated that all diggers be equally active and perform to their maximum ability: after soil deposition, each robot immediately returned to the tunnel to excavate. In the second protocol (Reversal, Fig. S8), the robots were similarly programmed to immediately resume excavation after deposition and were additionally given a reversal probability. In the third protocol (Lorenz, Fig. S9), we implemented an unequal probability to excavate derived from experimental ant workload inequalities.

We analyzed the global traffic dynamics of the robots in the main tunnel area using position tracking (supplementary materials, Fig. S11, see Fig. 4B-D for sample space-time overlap maps of robot positions). We found that traffic flow of robotic ants was similar to that obtained in the CA model and sensitive to the tunnel density, ρT (NT/LT, where NT is the average number of robots in the main tunnel area), maximal at an intermediate ρT, followed by a gradual decline at higher ρT (Fig. S12 A). Each digging strategy produced distinct trends in tunnel density and energy expenditure (Fig. S12 B). The Reversal strategy exhibited peak excavation performance with 2 robots, and monotonically increasing density and energy cost for trials with more diggers. The Lorenz strategy consistently resulted in low tunnel density and energy cost. Whereas, for the Active strategy, the addition of a fourth robot resulted in a dramatic decrease in density and increase in energy expenditure.

To understand these global traffic dynamics, we examined the dynamics of local robot clusters. We identified aggregations, defined as clusters of robots within a robot length’s proximity of each other, at each video frame. Multi-robot aggregations were common among all strategies and particularly frequent at the excavation site (histograms in Fig. 4B-D). To understand how clusters dissolved at the excavation site, we measured the mobility of each aggregation with a density overlap correlation function, Q(τ). This technique has been applied to the analysis of ant traffic (20), but is more traditionally used to examine dynamic heterogeneities in non-active matter such as soft matter systems (28). The metric Q(τ), derived here from image correlation algorithms used in PIV (29) (Fig. 4G inset, Fig. S13, supplementary materials), Q(τ) compares the spatial overlap of an aggregation at a specific time to the overlap of the aggregation’s original lateral segment at a later time, τ. We calculated the relaxation time, τ*, of aggregations of a specific number of diggers, N, by fitting a stretched exponential function, Q_f (τ)=e^({-(τ/(τ^(*)))^β }) , to a Q curve averaged over aggregations of the same N. For 3-robot trials, all strategies produced relatively low τ* regardless of N (Fig. 4F). However, the addition of a fourth robot dramatically changed the relative dynamics of the three strategies.

The Active strategy revealed how aggregation dissolution was sensitive to the confinement caused by the tunnel. In particular, larger N jams resulted in increasingly higher τ*. Thus, 2-robot aggregations led to 3-robot aggregations, which consequently led to catastrophic 4-robot jams that spanned the tunnel width. Such jams were difficult to resolve with the robots' limited library of maneuvers. Unlike ants, which can climb over each other and self-deform, the robots were limited to turning and reversing maneuvers, leading to collisions that were exacerbated by the robots' rigid oblique shape (Fig. 4E). We posit that this decreased maneuverability increased the penalty of congestion.

Surprisingly, the Reversal and Lorenz strategies generated unique mechanisms for mitigating catastrophic jamming despite the locomotive limitations of the robots. Due to the robots giving up excavation and returning to the tunnel exit after some time in a jam, the Reversal strategy established an upper limit on τ*, breaking the cascading chain-reaction effect observed in Active trials. The unequal workload distribution of the Lorenz strategy also avoided 4-robot aggregations, resulting in similarly low τ* as 3-robot trials. An analysis of relaxation times for clusters with similar aggregation density, ρ (N/L), during 4-robot experiments (Fig. 4H) revealed a sharp increase in τ* for the Active strategy past a local density of 1, reminiscent of glassy arrest in soft-matter systems (30). The Reversal strategy did not exhibit this glass forming characteristic, and a distribution of aggregation frequency vs ρ (Fig. 4G) revealed how the Lorenz strategy largely avoided high densities where catastrophic jams occur. In particular, robot inactivity under the Lorenz strategy actually resulted in overall increased efficiency of the collective. We argue that task-oriented active matter systems at high density must utilize similar social strategies to mitigate catastrophic long-time flow disruption.

Our robophysical experiments in concert with ant observations and CA simulations revealed how workload distributions and reversal behaviors of individual diggers resulted in emergent high-level regulation of density and traffic flow in the tunnel. Notably, the robots possessed no centralized controls. Instead, pre-programmed workload distributions served as feedforward prescriptions for controlling both local and global robot densities, whereby embedded idleness of individuals allowed the collective active matter system to reduce the occurrence of compromising clogging scenarios. The reversal strategy served as a simple feedback mechanism for controlling density by enabling the system to handle clogging scenarios more effectively. XX MAKE SURE WE CITE COUZIN + GARNIER PNAS 2015…THEY HAVE REFS TO TRAFFIC DENSITY OPTIMZASTION …OURS HAS GLASSY,,

For large population systems, the control templates discovered here may serve as effective bases for robust excavation, useful for future robotic systems that will aid in tasks like smooth caravans and carpools in autonomous vehicles, debris excavation and removal, mapping of complex terrain as well as lunar and asteroid mining (15). Even in the absence of complex protocols and sophisticated modes of locomotion, these classes of high-level strategies form a simplified syntax for engineers to modulate traffic in complex swarming systems, which can then be improved with refined protocols, body geometry, compliance and maneuverability. We posit that such a simplified language for collective control is crucial to traffic stabilization across physical and biological task-oriented systems, and particularly to the evolution of confined social colonies MAYBE CITE APPROPRIATE GORDON, PRATT PAPERS HERE.

Acknowledgements: Authors acknowledge the support of National Science Foundation grants number NSF PoLS 0957659, PHY-1205878 and also ARO W911NF-13-1-0347 and The National Academies Keck Futures Initiative. Authors would also like to acknowledge Dr. Nick Gravish for insight and fruitful discussions.

References:

1. M. C. Marchetti et al., Hydrodynamics of soft active matter. Reviews of Modern Physics 85, (2013).

2. S. Ramaswamy, in Annual Review of Condensed Matter Physics, Vol 1, J. S. Langer, Ed. (Annual Reviews, Palo Alto, 2010), vol. 1, pp. 323-345.

3. J. Palacci, S. Sacanna, A. P. Steinberg, D. J. Pine, P. M. Chaikin, Living Crystals of Light-Activated Colloidal Surfers. Science 339, 936-940 (2013).

4. A. Okubo, Dynamical aspects of animal grouping: Swarms, schools, flocks, and herds. Advances in Biophysics 22, 1-94 (1986).

5. Y. Katz, K. Tunstrom, C. C. Ioannou, C. Huepe, I. D. Couzin, Inferring the structure and dynamics of interactions in schooling fish. Proceedings of the National Academy of Sciences of the United States of America 108, 18720-18725 (2011).

6. W. Bialek et al., Statistical mechanics for natural flocks of birds. Proceedings of the National Academy of Sciences of the United States of America 109, 4786-4791 (2012).

7. A. Cavagna et al., Scale-free correlations in starling flocks. Proceedings of the National Academy of Sciences 107, 11865-11870 (2010).

8. M. Ballerini et al., Interaction ruling animal collective behavior depends on topological rather than metric distance: Evidence from a field study. Proceedings of the National Academy of Sciences 105, 1232-1237 (2008).

9. D. Helbing, Traffic and related self-driven many-particle systems. Reviews of Modern Physics 73, 1067-1141 (2001).

10. N. C. Darnton, L. Turner, S. Rojevsky, H. C. Berg, Dynamics of Bacterial Swarming. Biophysical Journal 98, 2082-2090 (2010).

11. E. Méhes, T. Vicsek, Collective motion of cells: from experiments to models. Integr. Biol. 6, 831-854 (2014).

12. A. Garcimartín et al., Flow and clogging of a sheep herd passing through a bottleneck. Physical Review E 91, (2015).

13. L. G.-B. Yash Mulgaonkar, Anurag Makineni, and Vijay Kumar, Bio-inspired Swarms of Small Aerial Robots (submitted). Interface Focus, (2017).

14. L. Wang, A. Ames, M. Egerstedt, paper presented at the 2016 American Control Conference (ACC), 2016/07 2016.

15. P. T. Metzger, Space development and space science together, an historic opportunity. Space Policy 37, 77-91 (2016).

16. L. Giomi, N. Hawley-Weld, L. Mahadevan, in Proc. R. Soc. A. (The Royal Society, 2013), vol. 469, pp. 20120637.

17. V. Linevich, D. Monaenkova, D. I. Goldman, Robophysical study of excavation in confined environments. Artificial Life and Robotics 21, 460-465 (2016).

18. D. Cassill, W. R. Tschinkel, S. B. Vinson, Nest complexity, group size and brood rearing in the fire ant, Solenopsis invicta. Insectes Sociaux 49, 158-163 (2002).

19. L. Lach, C. L. Parr, K. L. Abbott. (Oxford University Press (OUP), 2009).

20. N. Gravish, G. Gold, A. Zangwill, M. A. D. Goodisman, D. I. Goldman, Glass-like dynamics in confined and congested ant traffic. Soft Matter 11, 6552-6561 (2015).

21. D. Monaenkova et al., Behavioral and mechanical determinants of collective subsurface nest excavation. The Journal of experimental biology 218, 1295-1305 (2015).

22. P. Tenczar, C. C. Lutz, V. D. Rao, N. Goldenfeld, G. E. Robinson, Automated monitoring reveals extreme interindividual variation and plasticity in honeybee foraging activity levels. Animal Behaviour 95, 41-48 (2014).

23. E. J. Robinson, O. Feinerman, N. R. Franks, Flexible task allocation and the organization of work in ants. Proc Biol Sci 276, 4373-4380 (2009).

24. V. Fourcassie, A. Dussutour, J. L. Deneubourg, Ant traffic rules. Journal of Experimental Biology 213, 2357-2363 (2010).

25. C. Gershenson, D. Helbing, When slower is faster. Complexity 21, 9-15 (2015).

26. K. Nagel, M. Schreckenberg, A cellular automaton model for freeway traffic. Journal de Physique I 2, 2221-2229 (1992).

27. R. Kuhne, in Internation Symposium on Highway Capacity. (1991).

28. K. N. Nordstrom, J. P. Gollub, D. J. Durian, Dynamical heterogeneity in soft-particle suspensions under shear. Physical Review E 84, (2011).

29. Z. Jiang, Q. Kemao, H. Miao, J. Yang, L. Tang, Path-independent digital image correlation with high accuracy, speed and robustness. Optics and Lasers in Engineering 65, 93-102 (2015).

30. C. A. Angell, Formation of Glasses from Liquids and Biopolymers. Science 267, 1924-1935 (1995).
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

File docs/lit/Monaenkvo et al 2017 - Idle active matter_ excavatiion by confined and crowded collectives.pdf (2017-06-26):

Submitted Manuscript: Confidential 6 April 2017

Idle active matter: excavation by confined and crowded collectives
D. Monaenkova¹*, J. Aguilar²*, V. Linevich²

, W. Savoie¹

, B. Dutta¹

, M. A. D. Goodisman³
, D. I.
Goldman¹*.

1 School of Physics, Georgia Institute of Technology, Atlanta, GA, USA

2School of Mechanical Engineering, Georgia Institute of Technology, Atlanta, GA, USA

3School of Biological Sciences, Georgia Institute of Technology, Atlanta, GA, USA

*Correspondence to: daniel.goldman@physics.gatech.edu

†Additional author notes should be indicated with symbols (for example, for current addresses).

Abstract (100-150): Ensembles of self-propelling elements can spontaneously form clusters, clogs and jams. In some active materials, avoiding structure formation is important for task completion, for example, during nest formation by social insects. We studied biological and mechanical collectives, including fire ant colonies, cellular automata models, and autonomous robots, to demonstrate the importance of appropriate individual and group-wide behaviors in facilitating tasks by crowded, confined active matter. We used tools from the study of glasses and dense particulate ensembles to provide insight into mechanisms by which congestion, jams and even
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

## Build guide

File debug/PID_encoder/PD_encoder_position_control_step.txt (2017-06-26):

#define motorA1 51 //black wire
#define motorA2 53 //brown
#define motorA_PWM 4
#define encoder1PinA 2
#define encoder1PinB 3 
//#define Vpin            0                       // battery monitoring analog pin
//#define Apin            1                       // motor current monitoring analog pin

//#define CURRENT_LIMIT   1000                     // high current warning
//#define LOW_BAT         10000                   // low bat warning
#define LOOPTIME        100                     // PID loop time in milliseconds (unit check worked out)
//#define NUMREADINGS     10                      // samples for Amp average

//#define motorB1 55 //black wire
//#define motorB2 57 //brown
//#define motorB_PWM 8
//#define encoder2PinA 6 
//#define encoder2PinB 7

volatile long encoder1Pos = 0;                  //rev counter
//volatile int encoder2Pos = 0;

boolean A1_set = false;
boolean B1_set = false;
//boolean A2_set = false;
//boolean B2_set = false;

float pos_set = 15;                               // position (Set Point) (in revolution)
float pos_act = 0;                                // position (actual value) (in revolution)
int PWM_val = 0;                                // (25% = 64; 50% = 127; 75% = 191; 100% = 255)
float Kp =    16; //60;                                // PID proportional control Gain
float Kd =    400; //1200;                                // PID Derivitave control gain
float Ki =    0; //0.0001;
// values can be tuned farther
unsigned long lastTime;
float pidTerm = 0;                                                            // PID correction
float error=0;                                   
float last_error=0;   
float dErr = 0;      
double errSum = 0;
unsigned long cur_time;

void setup() {
  // put your setup code here, to run once:
  pinMode(motorA1, OUTPUT);
  pinMode(motorA2, OUTPUT);
  pinMode(motorA_PWM, OUTPUT);
  pinMode(encoder1PinA, INPUT); 
  pinMode(encoder1PinB, INPUT);
  digitalWrite(encoder1PinA, HIGH);                      // turn on pullup resistor
  digitalWrite(encoder1PinB, HIGH);                      

  // encoder pin on interrupt 0 (pin 2)
  attachInterrupt(digitalPinToInterrupt(2), doEncoder1A, CHANGE);
  
  // encoder pin on interrupt 1 (pin 3)
  attachInterrupt(digitalPinToInterrupt(3), doEncoder1B, CHANGE);

//  pinMode(motorB1, OUTPUT);
//  pinMode(motorB2, OUTPUT);
//  pinMode(motorB_PWM, OUTPUT);
//  pinMode(encoder2PinA, INPUT); 
//  pinMode(encoder2PinB, INPUT);
//
//  attachInterrupt(digitalPinToInterrupt(6), doEncoder2A, CHANGE);
//
//  attachInterrupt(digitalPinToInterrupt(7), doEncoder2B, CHANGE);

  Serial.begin (9600);
}

void loop() {
  // put your main code here, to run repeatedly:
//  getParam();                                                                 // check keyboard
//  if((millis()-lastMilli) >= LOOPTIME)   {                                    // enter tmed loop
//    lastMilli = millis();
//    getMotorData();                                                           // calculate speed, volts and Amps
//    PWM_val= updatePid(PWM_val, speed_req, speed_act);                        // compute PWM value
//    analogWrite(motorA_PWM, PWM_val);                                              // send PWM to motor
//  }

  cur_time = millis();
  Serial.print(cur_time); Serial.print(" "); Serial.print(pos_set); Serial.print(" ");
  pos_act = (encoder1Pos)/(48*74.83); // outputs current position in terms of revolution
  Serial.println(pos_act);
//  Serial.print(pos_act); Serial.print(" ");
  PWM_val= updatePid(PWM_val, pos_set, pos_act);
//  Serial.println(PWM_val);

  if (PWM_val >= 0){
    digitalWrite(motorA1,LOW);
    digitalWrite(motorA2,HIGH);
    analogWrite(motorA_PWM,abs(PWM_val));
  }
  else {
    digitalWrite(motorA1,HIGH);
    digitalWrite(motorA2,LOW);
    analogWrite(motorA_PWM,abs(PWM_val));
  }                                                
 
}

// Interrupt on A changing state
void doEncoder1A(){
  // Test transition
  A1_set = digitalRead(encoder1PinA) == HIGH;
  // and adjust encoder1Poser + if A leads B
  encoder1Pos += (A1_set != B1_set) ? +1 : -1;
}

// Interrupt on B changing state
void doEncoder1B(){
  // Test transition
  B1_set = digitalRead(encoder1PinB) == HIGH;
  // and adjust counter + if B follows A
  encoder1Pos += (A1_set == B1_set) ? +1 : -1;
}

int updatePid(int command, float targetValue, float currentValue)   {             // compute PWM value
  unsigned long now = millis();
  double timeChange = (double)(now - lastTime);     
    error = targetValue - currentValue; 
    errSum += (error * timeChange);
    dErr = (error-last_error);// / timeChange;
    pidTerm = (Kp * error) + (Kd * dErr) + Ki * errSum;    
//    Serial.print(error); Serial.print(" "); Serial.print(dErr); Serial.print(" ");
//    Serial.print(Kp*error); Serial.print(" "); Serial.print(Kd*dErr); Serial.print(" "); Serial.print(Ki*errSum);Serial.print(" ");
//    Serial.print(error); Serial.print(" "); Serial.print(last_error);Serial.print(" "); Serial.print(dErr); Serial.print(" ");
    last_error = error;
    lastTime = now;
    return constrain(command + int(pidTerm), -255, 255);          
  }

//void doEncoder2A(){
//  // Test transition
//  A2_set = digitalRead(encoder2PinA) == HIGH;
//  // and adjust counter + if A leads B
//  encoder2Pos += (A2_set != B2_set) ? +1 : -1;
//}
//
//// Interrupt on B changing state
//void doEncoder2B(){
//  // Test transition
//  B2_set = digitalRead(encoder2PinB) == HIGH;
//  // and adjust counter + if B follows A
//  encoder2Pos += (A2_set == B2_set) ? +1 : -1;
//}

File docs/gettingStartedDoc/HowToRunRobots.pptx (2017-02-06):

## How to run ant digger robots

QuickStart Guide

## About Arduino IDE

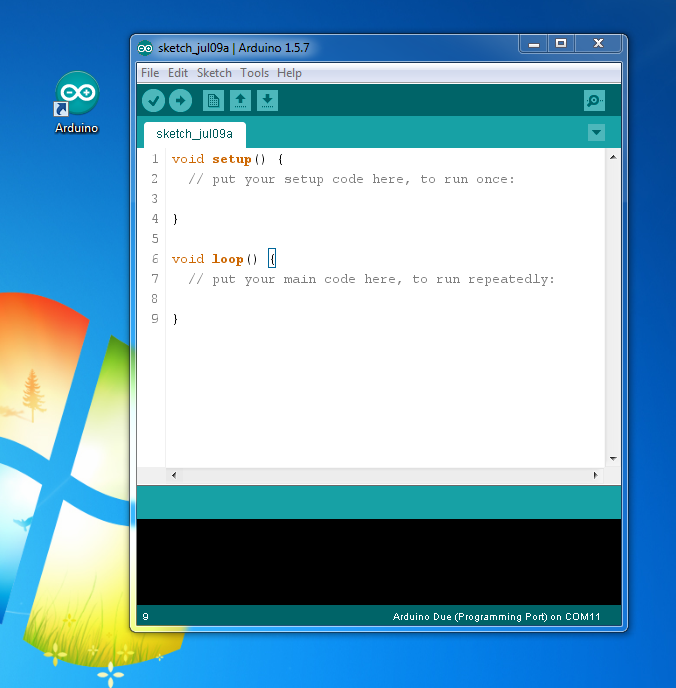
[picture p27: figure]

- Can be opened by clicking Can this icon
- This button will compile the current C/C++ code and check for errors
- This button will compile and upload current code to the connected Arduino board

## Connecting Arduino to PC

USB Cable connected to Arduino DUE

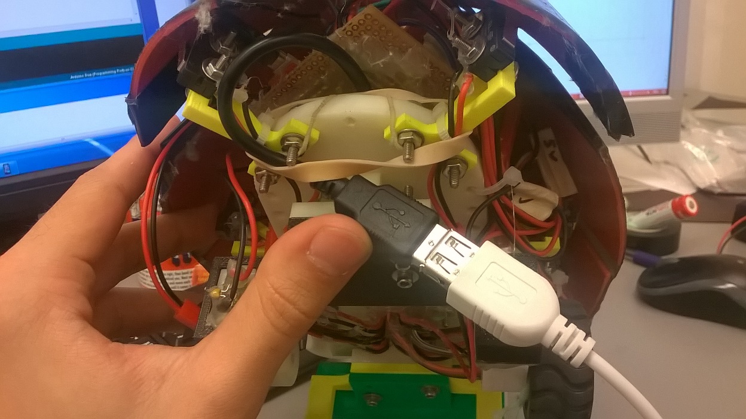
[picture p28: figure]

USB extension cable, goes to PC USB port

- Look for a male USB connector underneath the robot. Use a USB extension cable

## Set up Arduino IDE to properly talk to robot

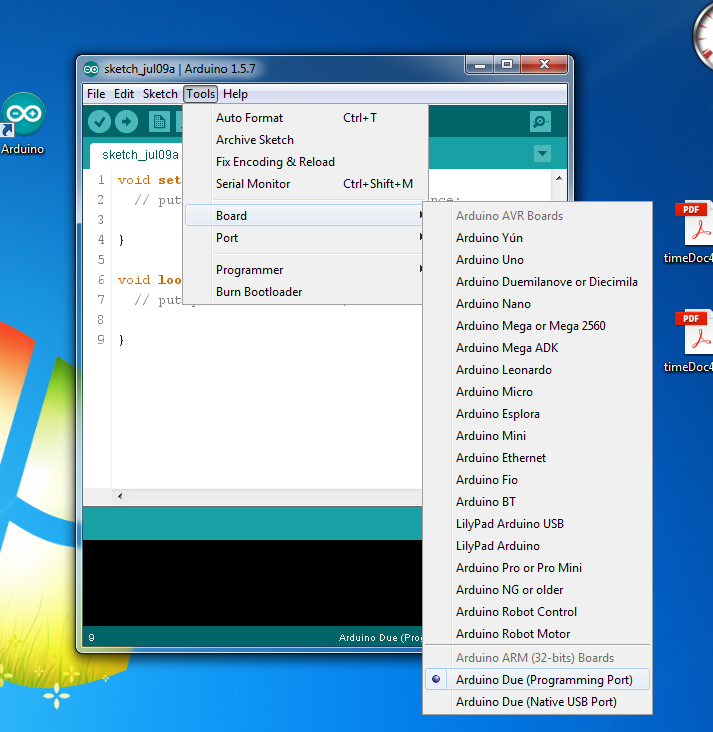
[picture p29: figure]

- Go to Tools > Board > Arduino Due (Programming Port). We need to tell the IDE which board is connected so that the code can be properly compiled. It should say “Arduino Due Programming Port” here when done.

## Check if PC sees your board on COM port

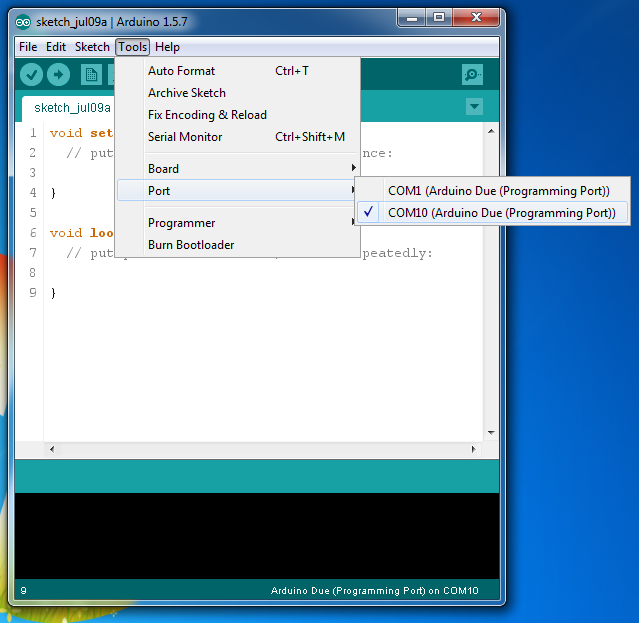
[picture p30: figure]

Go to Tools > Port >
Look for a COM port (not COM 1)

## Not sure which COM port?

STEP 2

STEP 1

Click on Device Manager

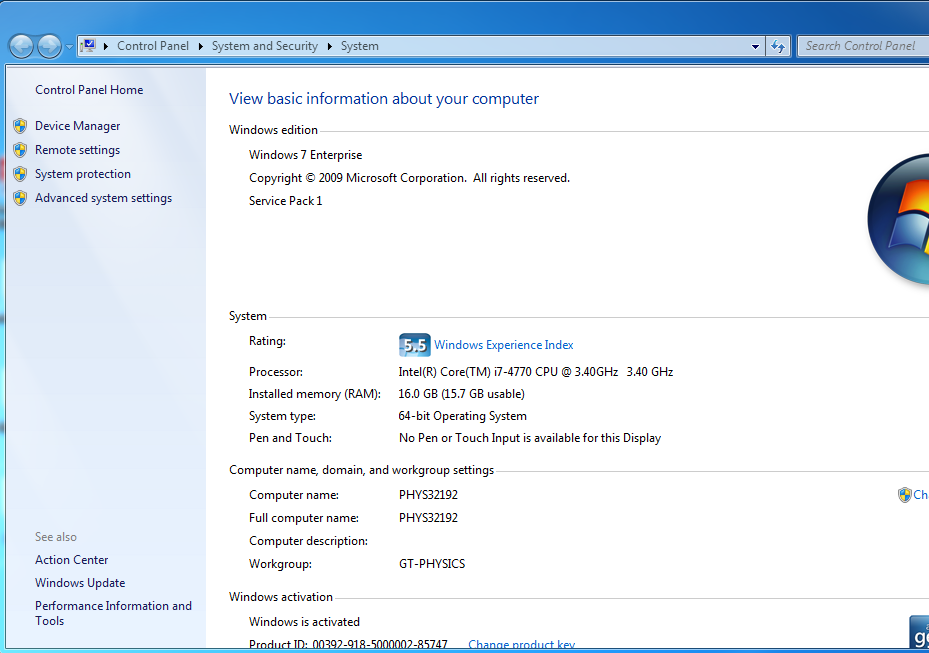
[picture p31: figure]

- Go to Device Manager. In the explorer, left click on computer > Properties

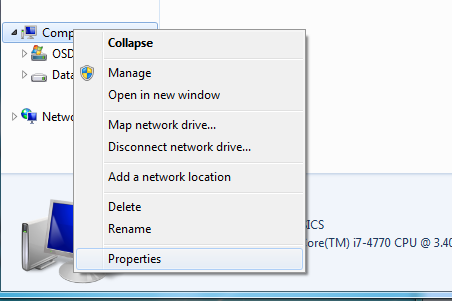
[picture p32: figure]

## Not sure which COM port?

STEP 3

- Look for your Arduino Board

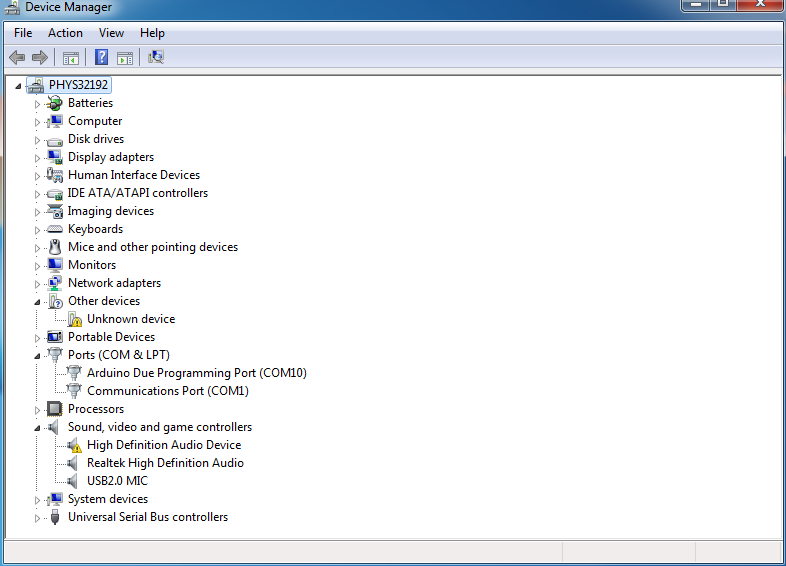
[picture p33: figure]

## If the Arduino Doesn’t show up on the COM

- Unplug the USB connection from the computer, plug it back again.
- Try it several times, it will work.
- If not, drivers may be corrupted and will need to be reinstalled. Very unlikely. Refer to forums. (Maybe ill add a tutorial later)

## Uploading a code to the robot

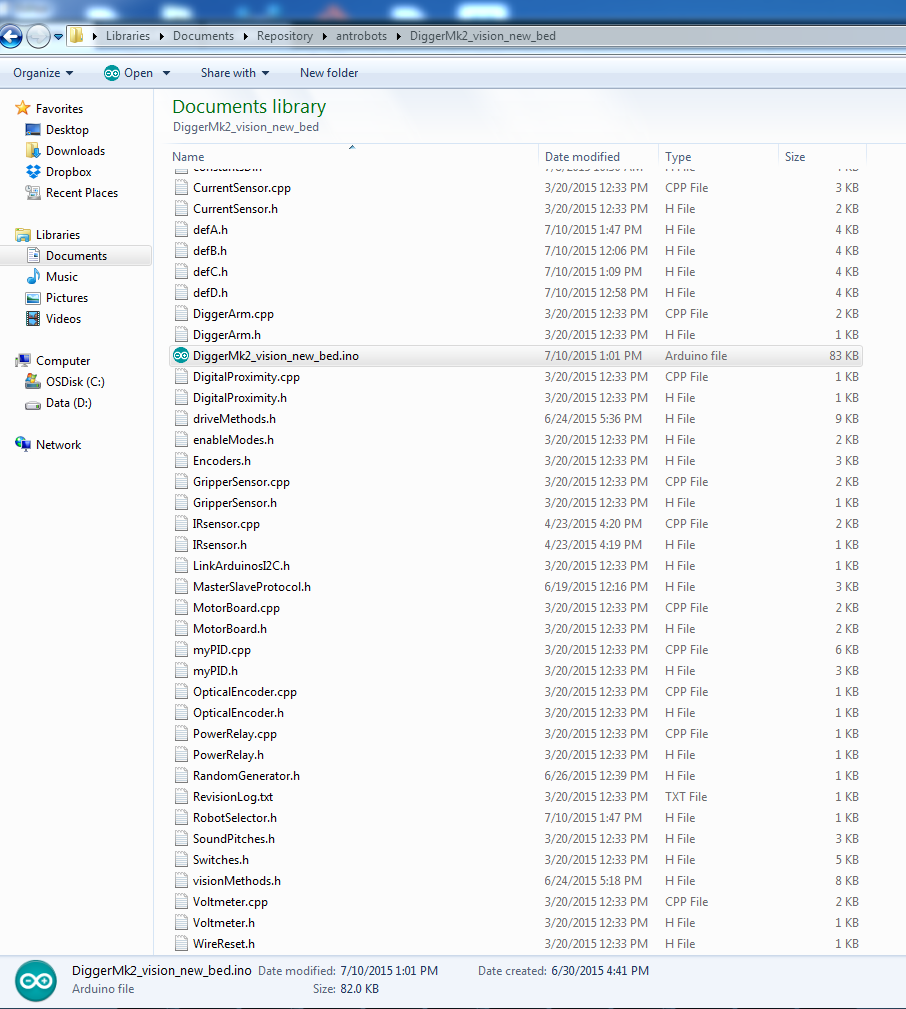
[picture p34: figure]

- Go to Documents > Repository > antrobots > DiggerMk2_vision_new_bed folder
- Find DiggerMk2_vision_new_bed.ino file. There should be only one file with .ino extension. Open it.

## You should see this window

- Note how the canvas is grayed out. This is because in the File> Preferences “use external editor” option is enabled. This prevents us from using Arduino IDE itself to edit the code and just use the IDE to compile and upload code
- Since the, I code is long and complicated suggest using Notepad++. Its easier and more convenient to navigate around
- Having external editor option checked will make sure that the code is reloaded into the IDE from the disk before compilation

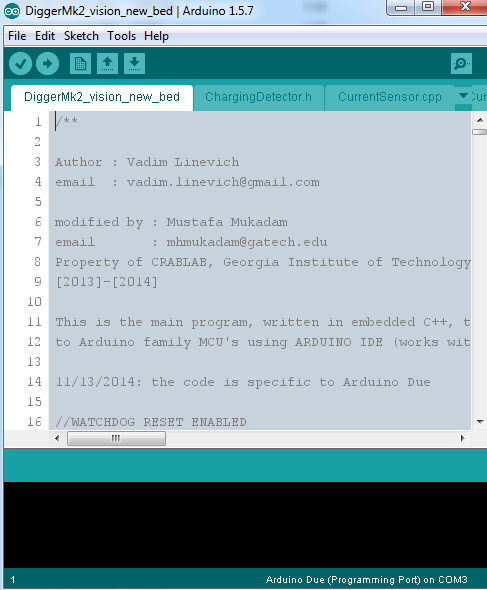
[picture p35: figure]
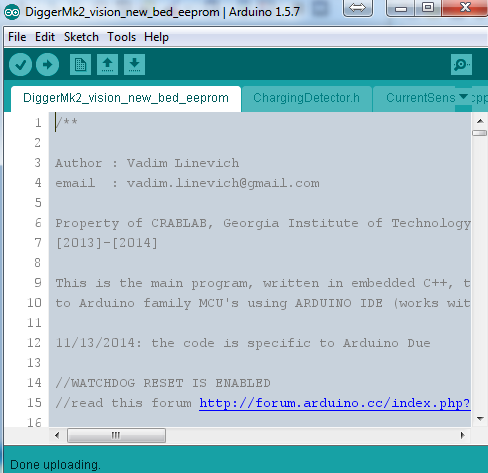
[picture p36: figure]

For Lorenz+hold switch key when start

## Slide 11

- I like editing the main code (DiggerMk2_vision_new_bed.ino) with Notepad++, that’s why I have a check box “use external editor” enabled in the Arduino IDE.
- If you open the main file with Notepad++, you should see something like this

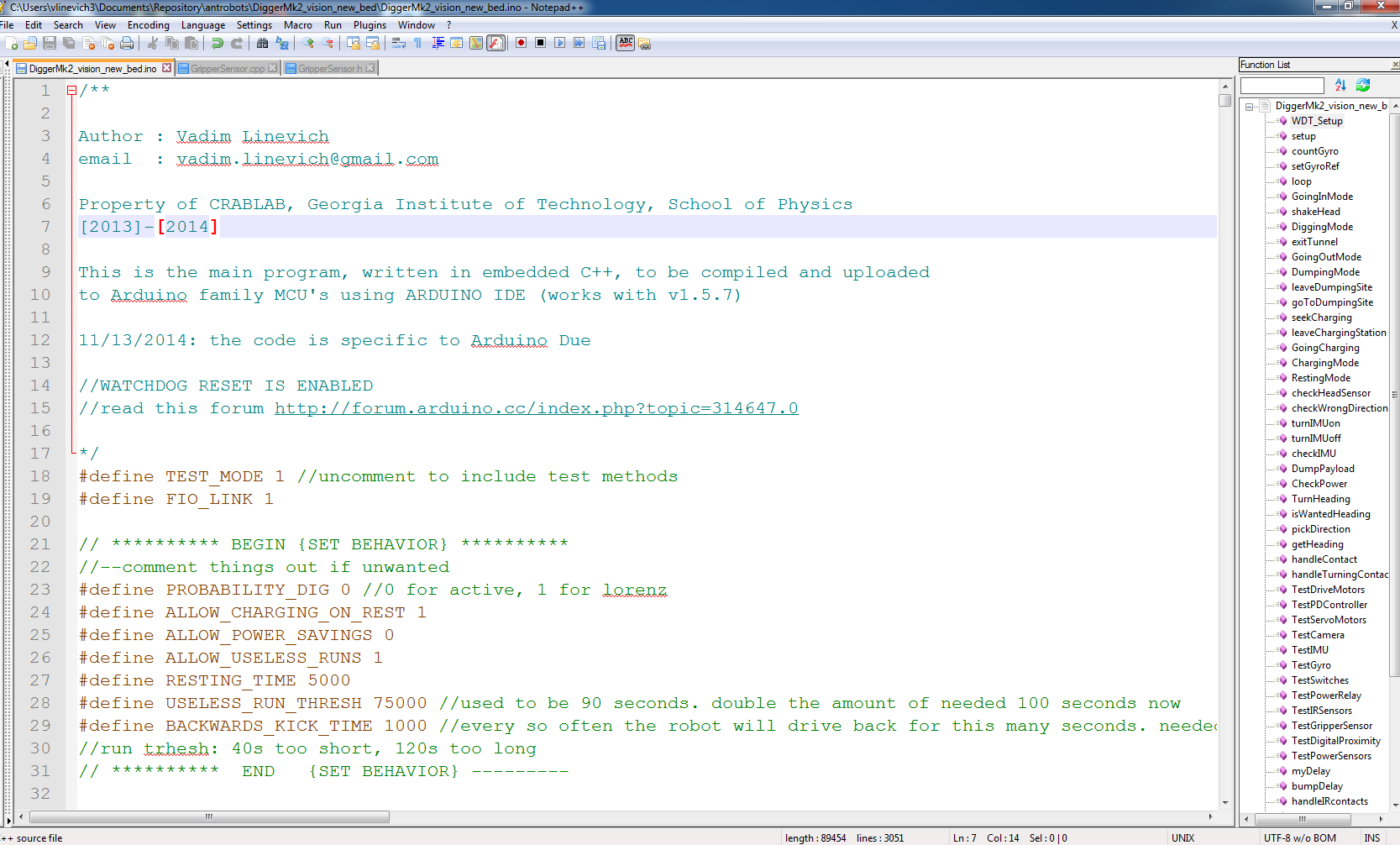
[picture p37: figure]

My contact info

## This is probably the only thing that you may want to tweak

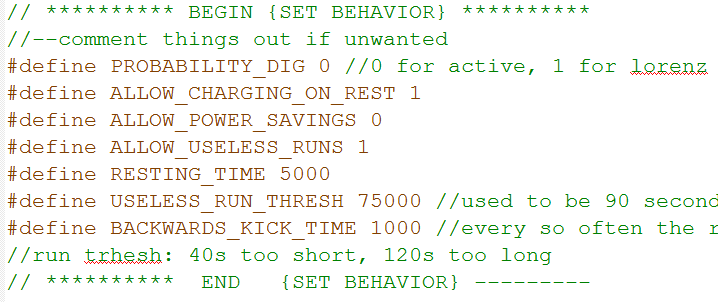
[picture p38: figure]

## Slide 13

- Each robot has a set of its own configuration files: “constantsX.h” and “defX.h” where X could be A,B,C,D (to represents four robots named A,B,C, and D).
- “def.h” tells the software how the hardware and sensors are connected, plus some convenience macros. Don’t worry about(or mess with) these unless you really know what you are doing.
- “constants.h” contains various tunable constants. For example, it will tell the robot compass directions, PID controller gains, base velocity and such. This is where you would set Lorenz probability distributions. I would not recommend to mess with anything else.

## How to program a robot

Establish a USB connection with a robot and figure out which COM port its connected to

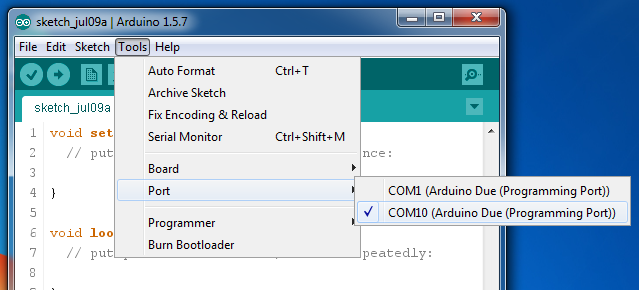
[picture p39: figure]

This robot was set to connect to COM10

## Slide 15

- Now open RobotSelector.h and look for a robot name which matches given COM port name

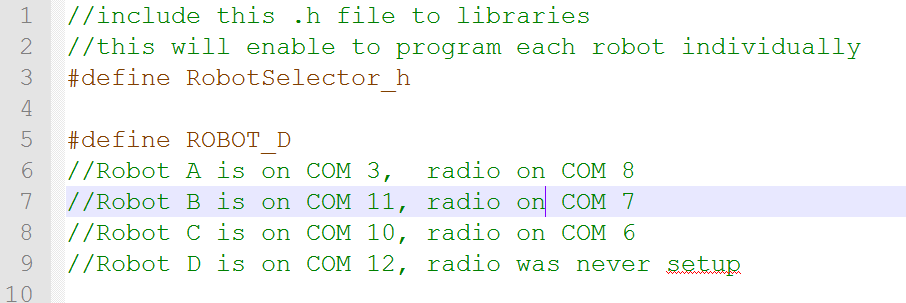
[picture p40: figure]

Once you select (or define) a correct robot, SAVE this file.

COM 10 implies that we need to change line 5 to
#define ROBOT_C

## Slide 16

- If you have Probability Digging enabled (#define PROBABILITY_DIG 1 ), set correct probabilities for each robot that you are programming. This is done in “constantsX.h” file.

GO_DIG_PROB specifies a probability chance (in percent) for a robot to go dig after making a deposit. Make sure that GO_DIG_PROB + GO_REST_PROB = 100

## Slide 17

- When done press upload button

## Modified Lorenz

- 1) Small switch to start logging data
- 2) Large switch to give power to the robot
- 3) Wait until head moves
- 4) Press white reset button (the robot will loose power and the camera light will restart)
- 5) Wait for the head to move again
- 6) Hold dumping switch
- 7) Wait for the light on the camera to go off
- 8) Release the switch

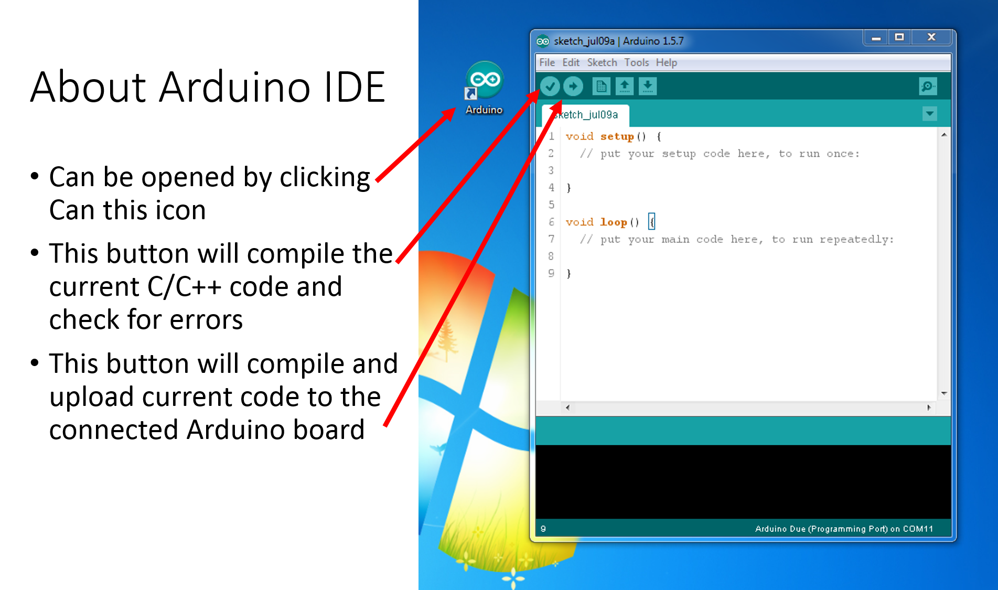
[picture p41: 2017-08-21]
docs/gettingStartedDoc/pic1.png

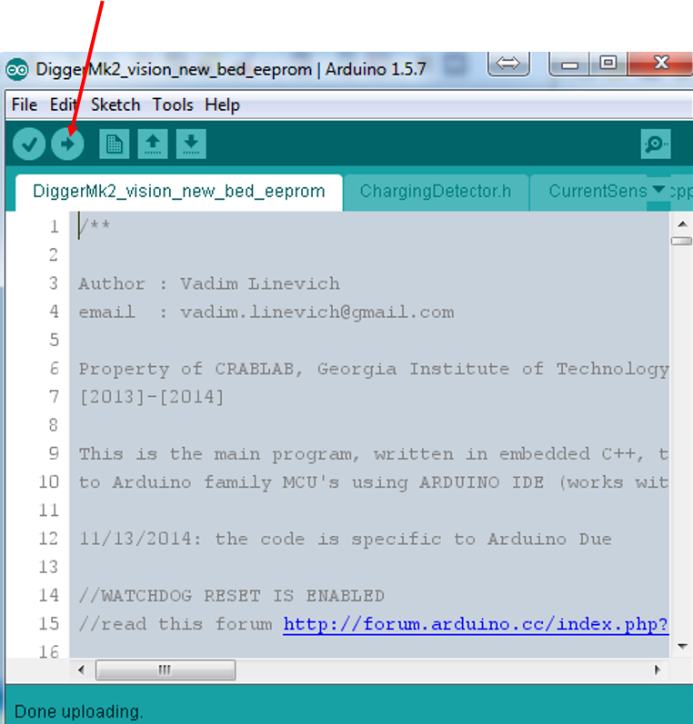
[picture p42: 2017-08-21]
docs/gettingStartedDoc/upload.png

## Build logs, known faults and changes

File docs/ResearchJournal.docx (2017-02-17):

Date: September 27, 2016

This serves as an e-introduction among all of us—Magnus and I are interested to see if his swarm work can be integrated with our ant robot work to learn if collisions among densely packed task oriented collectives of robots can be used to ensure good flow, etc. I suggest that all the students and postdocs cc’d on this email self-organize to trade info on what we (they) are doing and then in the coming weeks we can all meet to see if anything emerges,

The new research direction on using ant-inspired collisions in swarm robot control/localization seems very interesting.

Date: October 4, 2016

Grad Groups meeting today featured a woman from the library who overviewed the different resources available to graduate students. For research in engineering, she recommended compendex and inspec as good databases.

Date: October 5, 2016

I was supposed to have a Skype call with JSP today to review the robotic ant systems, but he was not able to get online. Instead, we chatted on the phone, and I took down the following notes:

Mechanically it is sort of sorted out

- Two of them are not working well (Echo and Charlie?)

When you connect the batteries, you need to separate the batteries completely off of the wires

Issues are not commented within the code

I also spent a good amount of time today studying the codebase and learning its architecture. I think I have a good understanding of it, and I love the thorough documentation. I am not sure I understand the Watch Dog Timers (WTD), and I haven’t found a satisfactory explanation of them online. I would love an explanation of them from JSP.

Date: October 6, 2016

I continued reviewing the code, and Dr. Goldman showed me how to turn on the robots. There is a black switch on the side which turns it on and off, as well as a button on the main board which can be used to reset the robot.

All of the batteries were dead, so there are two things that I need to do to get started:

1. Learn how to charge the batteries
2. Make a power cable so that the robots can run off of a power supply (3.6V).

Date: October 6, 2016 - Update

I made a power cable to hook up to the power supply, but the power supply did not provide a high enough current to power all of the systems on the robots. I had asked Will to show me how to charge the Li-Ion batteries so I could charge them while I worked on the cable, so we were able to plug them into the battery cartridge. I also tested each of the robots with fresh set of batteries to see if they were operational, and have started a Google Sheet (https://docs.google.com/spreadsheets/d/13Cs-2KYUY0CCcL2nHpb5zxYH1IgCLRBWxw0L3XnAVaY/edit) to track the health of each robot over time.

Date: October 7, 2016

11:00AM - Will mentioned to me yesterday that the recharging process while the ants are running is not a straightforward process, and there are several files floating around on the lab desktop with tables I think might be necessary for regulating the charging method. See “C:\Users\vlinevich3\Desktop\Charging MPR121 Program vals.xlsx”.

12:00PM - Continued going through the documentation left by JSP and fleshing out the Robotic Ant Status (https://docs.google.com/spreadsheets/d/13Cs-2KYUY0CCcL2nHpb5zxYH1IgCLRBWxw0L3XnAVaY/edit) to get a better feel for the architecture and pre-existing problems. I also started up a Trello Board (https://trello.com/b/C5Ynd05Q/georgia-tech-research) to track proposed changes from JSP. The Trello board is populated with the “List of things that need to be done in the future” in the Ant Robot Mk.2 Software Documentation (https://docs.google.com/document/d/1-CU7JS0_f5LQ8yZ_QIc0lyrAXqRvDMj-JCnnrbyMqyo/edit)

4:00PM - Calling it a day. Feeling better about navigating the code. There seems to be some extraneous stuff left over from previous iterations, but I’d prefer to just get things running for now before going back and modifying working code to basically just look pretty. Best practices can be implemented after I have proven that I can get data with what we have right now.

I was hoping to hear from JSP today, but I might just shoot him an email with all of my documented questions later tonight.

Date: October 10, 2016

Notes from my conversation with JSP and Bahni.

Questions for JSP:

1. Where is the correct code?
  a. In JSP folder like Bahni showed you.
2. Upload process?
  a. Straightforward
3. Where is data stored and how do I retrieve it?
  a. Need to communicate with the Fio board, due to the lack of available pins on the Due. Talk to Bahni about this
4. Will mentioned to me yesterday that the recharging process while the ants are running is not a straightforward process, can you tell me about the recharging procedure and what I need to do to make sure everything is properly tuned?
  a. Bahni knows how to do this.
5. Debugging process? I am guessing I can get a lot from the data logging capabilities of the system
  a. Write data to Fio
6. I was going through the code, and I found a few lines pertaining to an LSM9DS0 (https://learn.sparkfun.com/tutorials/lsm9ds0-hookup-guide/introduction), which wasn’t on the inventory list, and I wasn’t able to find anything on the robots which looked like the board in its documentation. Is this code from a previous version...have I even been looking at the right code?
  a. You have, there is just a lot of old code leftover from previous iterations
7. Watch Dog Timer? Is this a deprecated thing now?
  a. Still needed. Maybe a bit messy, but it gets the job done.
8. Recommended steps from JSP:
  a. Turning behavior needs the most work
  b. Focus on getting the IMU working
    i. Two modes:
      1. Magnetic field tells heading
      2. Using gyroscope to tell degrees of rotation
        a. Used to turn, but neither seems to work
  c. And get to know the hardware
  d. Resetting behavior is a minor issue

Methods

TurnHeading - mainly for turning from one direction to another (180 deg). If preferGyro is true, then it will use the gyro readings to turn. If it is false, then it will use the magnetic fields heading to determine the heading of the robot as it turns. Neither of them seem to work.

Set charging station to 4.2 volts

PID needs some work, but Vadim is a better source than JSP.

PixyCam doesnt have a large enough field of vision. Modify the mount to make this better.

CapacitiveSensors should be reliable. The point is that we want to distinguish the wall from the other ant robots. Capacitive sensors charge and discharge the copper pads on the robot. If the time to charge changes, it can detect if it’s touching, and if it is, what type of material it is touching. When you connect it to a common ground, then the readings from the sensors will be totally different.

Antcomm lets you communicate with integers fiowriteint

repository/antorobots/FioWirelessV4

Clicking motion is a reset indication.

Date: October 11, 2016

10:00AM - Working on re-uploading the code to the robots which stall in Going In mode (Alpha and Echo). Method given below.

Uploading software to Robot Ants

Uploading to the Fio Board (https://www.arduino.cc/en/Main/ArduinoBoardFioProgramming)

1. Unplug the 3.3V wire which goes to the LCD from the FTDI pins on the left side of the robot.

There are two arduino board on the robot ant platform (Due and Fio). Open the FioWirelessV4.ino in >> repository/antorobots/FioWirelessV4 in the Arduino UI and make sure that Tools>Board>Arduino Fio is selected. Verify the sketch.

What is the intended reset switch behavior?

11:30AM - Uploaded software to both non-operational robots and their behavior did not change. Next step is checking the constants files for each robot.

Both robots which do not work have low Kp values (Alpha = 1.5 and Echo = 0.75) compared to the working ones (Bravo = 2.5, Charlie = 2.5, Delta = 2.0). I increased the constantsA.h Kp values up to 2.5 and 3.5 and did not see any changes. Afterwards I returned the Kp values to the original values.

In constantsA.h, I updated OUT_DIRECTION from 270 to 291 and updated STARBOARD_DIRECTION from 170 to 200.

2:00PM - For Charlie, I am looking at the issues for the IMU.

dog.my ranges from 3100 to 9200 (always positive)

dog.mx takes on values in the range of -1500 to 200

To get familiar with the hardware, I am going to run through all of the testing methods in Robotic Ant Status (https://docs.google.com/spreadsheets/d/13Cs-2KYUY0CCcL2nHpb5zxYH1IgCLRBWxw0L3XnAVaY/edit).

3:00PM - TestSwitches is not producing any output for Charlie.

3:45PM - After a bit of tinkering I was not able to produce any output, but this may be correct. JSP showed Bahni and I some slides yesterday which demonstrated that the capacitive charges vary depending on whether or not the robot is powered by USB (something about common ground?). I removed all test cases and ran Charlie in the test bed, and the Fio serial output reflected all touches I introduced.

4:00PM - TestSwitches looks like it is deprecated and I should have been using TEST_CAP instead. Whoops :/

5:00PM - Calling it a day. I need someone to explain getDetectedContacts to me. I think I get the idea behind the if/else statements, but the meaning of switchState and the bitwise OR operations is lost on me.

Date: October 12, 2016

I have two big exams tomorrow, so I am not planning to do much today. Vadim gave us some input on the PixyCam regarding whether or not we should move to a different camera. We will need more processing power to use a webcam, because we will be required to handle the image processing onboard as opposed to on the camera itself like on the Pixy. He also recommended we use some sort of version control, which I am super happy about. When I asked the other members of the group why they didn’t use it, I think they were just scared to change over and opted to just keep making copies on the desktop. So the main task of the day is getting the files on my computer and then starting a git repository using GT Github Enterprise (https://support.cc.gatech.edu/support-tools/faq/what-gt-github-enterprise).

There is a single repository for this project, with two directories, one for the Due and one for the Fio. In addition, there are a number of dependencies on external libraries found in the Documents/Arduino/libraries directory. The best solution I can think of it just having everyone install these themselves, due to the fact that I am not sure how a repository of libraries would affect the other libraries other people already have.

Private repository is set up here. (https://github.gatech.edu/rwarkentin3/ant-robots)

Date: October 13, 2016

After the exams I came in for 3 hours and was working on getting the Github enterprise thing set up. It was a little messy with the security things in place, but I think it is all sorted out. I have the software running on both my laptop and the lab machine. Version controlled code on the lab machine is in Documents/Github/ant-robots

Date: October 14, 2016

I believe JSP said that the IMU issues popped up all at once, which makes me think that a software bug popped up during development that led to some IMU sensor data being interpreted incorrectly. There are several backup files saved to the desktop, and I am going to go through each one to see if there are any changes in the files dealing with the IMU that may be the source of this incorrect behavior.

There is lots of IR sensor stuff in the code, but it is all commented out. Are there even IR sensors on these robots anymore? Ask bahni…

Got side tracked and ended up reformatting a lot of the test code. Now the variables which activate the test loops are in a file called TestVals.h. I think it would be a good idea to remove the actual test methods from the .ino files and move them into their own .cpp file. In addition, it might be a good idea to move the TestVals.h data into RobotSelector.h and renaming to something like RobotSetup.h so that you only have to modify a single value prior to compiling your code.

I found an infinite loop in due_digger_mk2.ino that looks like it is intentionally forcing WDT to restart? Doesn’t seem like the best way to handle a hang.

numOfConsequitiveBackwardKicks is initialized all over the place but never used.

Date: October 17, 2016

Populated the Issues section of the ant-robots repository on GitHub, so the Trello board is a bit obsolete and out of the way.

10:30AM - Added parts documentation files. Eventually would like to add stuff like this to a Wiki to make it easier to access.

11:00AM - Added testing directions to the GHE wiki.

1:00PM - fioWrite() vs fioWriteInt() in due_digger_mk2/LinkArduinosI2C.h?

2:30PM - Committed a change to the test_branch repo that uses the enumerated testing method.

4:45PM - Bravo works well. The screws which attach the claw to the servo motor fell out, so I had to do some tinkering to get everything attached. The claw seems to be operational now, and I mounted the claw on Bravo so that they cannot fall out again.

Date: October 18, 2016

Running lots of tests with TEST_TURN_HEADING

Date: October 19, 2016

Look up code reference on line 2217. dof.gz is the rotational acceleration about the z-axis?

preferGyro is set to true on line 906 if there is something in the payload. Is this why turn heading seems to work dring going in but not during going out?

This might explain the issue with the LSM9DS0: https://forums.adafruit.com/viewtopic.php?f=19&t=66571

So the LSM9DS0 on Bravo stopped working for a little while. I found that I was able to fix it by uploading code with all power supplies unplugged, and then by...honestly, I don’t know. Resetting seems to help sometimes. I think there is an issue with power.

Date: October 20, 2016

Things I want to understand:

- checkWrongDirections() method
  - Returns a boolean value which is not used...see comments added above method in code
- where is current_target_heading used
- why is turnHeading() present?
  - As best I can figure, it is a hard coded method that will turn the robots around 180 degrees.
- What is the constant numOfConsequitiveBackwardKicks?
- FollowLane()
  - Is a method in driveMethods.h. It polls the camera for data using getDetectedSigs() and moves forward if the size of the pheromone area is greater than a certain threshold (fixed at 150 in the method).
- getDetectedSigs()
  - Is a method in visionMethods.h. It is a method that declares storage space and clears previous information, and performs filtering of incoming detected color data where only the biggest block of each color signature is detected returns pointer to an array struct.
- checkHeadSensor()
- Is exitTunnel() ever called? What is the difference between this method and goingOut()?
- Is nextMode variable variable necessary (see line 922)?

Added a serial output in FollowLane() with indicated if the area of the pheromone trail is not large enough to move forward.

Date: October 21, 2016

Problem with IMU didnt’t exist until capacitive sensors were implemented. Consider turning this sensing system off and checking IMU functionality again.

Car is dead. Got to leave early to work on it.

Date: October 23, 2016

Spoke with JSP:

  a. C:\Users\vlinevich3\Desktop\JSP - Back_UP_051916\DiggerMk2_vision_new_PhysicsLabSetUp
  b. Draining out the the batteries seems to help
  c. Turn on comm line, then turn on robot.

Date: October 24, 2016

IMU readings for robot are different depending on whether or not the USB is plugged in?

Raised the IMU higher off of the robot and the IMU testing gets better. Dropped it down and now it seems fine. Maybe one of the wires was loose?

Pulled enough cotton out of the wheels of Bravo to make a troll doll.

TurnHeadingRoss() is working. ExitTunnel() -> GoingOutMode() and handlingContacts is a little weird. Work on this stuff.

Date: October 26, 2016

The robot can dump!!! The second time it goes to dig, the robot seems to undershoot the bed when it attempts to grab the granular material. Not sure what that is.

Dr. Goldman and I observed a digging/leaving cycle, and he made a comment about the PID controller looking poorly tuned in during goingOutMode. I agree with his observation, but the robot works fine during goingInMode and I don’t think that the PID parameters change. Dr. Goldman suggested I reach out to Vadim and ask him about the PixyCam and look at the PixyCam software, and mentioned that I might need to re-tune the camera on Bravo (I think this is necessary for one of the other robots as well).

Lastly, Dr. Goldman asked about the power supply. I have only been testing the robots with fully charged batteries (~4.2V) and the robots seems to operate underpowered. It may be a circuitry thing, but I think there is just a lot more hardware on the robots than was originally planned for.

Date: October 27, 2016

http://cmucam.org/projects/cmucam5/wiki/Porting_Guide

http://cmucam.org/projects/cmucam5/wiki/Hooking_up_Pixy_to_a_Microcontroller_like_an_Arduino

Says Data out port should be set to 2, not 0 or 4 like you had…

So I found some files in Desktop/antrobots_2.0 that are config files for the firmware on the Pixy. I uploaded the most recent version “roboJSP.prm” and the robot started working again. Part of this sets the Data out port to 3…yeah...that goes against everything in the documentation, but whatever works.

Car battery needs to be replaced and I have a RoboJackets meeting in the early afternoon, so I gotta leave early and probably won't get back in time.

Date: October 28, 2016

Ended up having to go in this morning to get my car battery replaced, so I came in late today. Yesterday I found that the documentation for the Pixy does not line up with the software leftover from JSP which allows the robot to receive input from the the Pixy.

The Out data port is 3, when UART comm should be on 2. This could be the result of several issues:

1. The Pixy is hooked up incorrectly to the Due.
  a. Checked this. The Pixy pins are correctly connected to the Arduino according to the UART setup described here (http://cmucam.org/projects/cmucam5/wiki/Porting_Guide).
  b. If you open up PixyMon and try to configure a device, you can hover over “Data out port” on the Interface tab. This will display a comment which indicates that 3 is for UART.
2. The firmware for the Pixy has changed and the documentation does not reflect it.

I have downloaded all of the released firmwares, and want to test each firmware release with each of the .prm files I found to see which one operates best. This may allow me to observe the effects of firmware change on parameter processing.

In addition, the lens on the PixyCam can be focused. I may look into playing with this today after the firmware evaluation.

| pixycam.prm | roboVadim.prm | roboJSP.prm
firmware-1.0.2beta | Not tested | Not tested | Not tested
pixy_firmware-2.0.5 | Not tested | Not tested | Not tested
pixy_firmware-2.0.8 | Digs well, but gets frozen in Going Out mode. | Digs well, but gets frozen in Going Out mode. | Digs well, and performs the best of the parameters for pixy_firmware-2.0.8
pixy_firmware-2.0.12 | Not tested | Not tested | Not tested
pixy_firmware-2.0.17-general | Not tested | Not tested | Digs well, and perf orms the best. Currently on board.
pixy_firmware-2.0.19-general | Not tested | Not tested | Not tested

I have opted to use the most current firmware (pixy_firmware-2.0.17-general) with roboJSP.prm

I think that the robot freezes when there are not any pink blocks registered in the camera. I can “unfreeze” the robot by waving my rather pink hand in front of it...I should get outside more…

The first thing I want to do is see if the PID parameters are different for the GoingIn and GoingOut states. The GoingIn path following is very good, while the path following for GoingOut is poor.

Date: October 30, 2016

GoingOutModeRoss is the same as GoingInMode (the original method), with some slight modifications to handle behavior switching, but all in all everything is the same. I developed a test for the PID controller and will work on evaluating the output of the camera readings.

Date: October 31, 2016

Trying to figure out what is going on with the PID controller.

I have disabled the checkHeading method in goingOut mode, so it should just follow the lane and handle contacts, but it still exhibits overshoots and pivoting.

Test 1. So I disabled the checkHeading method in goingInMode, and initialized in goingInMode and it was able to follow the lane in both directions with the .prm file I made. Yay!...why?

Test 2. So I copied goingInMode into goingOutModeRoss and disabled the checkHeading method. I initialized in goingInMode, but in loop(), if goingIn is true, we go to goingOutModeRoss instead of GoingInMode. This approach also tracks the pheromone trail both directions!

Test 3. Initialize the robot in GoingOutMode.

Everything is the same except for if we start with enable_GoingInMode() or enable_GoingOutMode(). Both switch cases call GoingOutModeRoss() with the checkWrongDirections commented out.

enable_GoingInMode() with checkPayload() if-statement commented out works.

enable_GoingOutMode() with checkPayload() if-statement commented out does not work.

enable_GoingInMode() with CONTACT if-statement commented out works.

enable_GoingOutMode() with CONTACT if-statement commented out does not work.

enable_GoingInMode() with DUMPING_SWITCH if-statement commented out works

enable_GoingOutMode() with DUMPING_SWITCH if-statement commented out does not work

Everything but followLane commented out:

enable_GoingInMode() … doesn’t work! That is sort of progress

enable_GoingOutMode() … doesn’t work!

enable_GoingInMode() with CHARGER if-statement commented out works

enable_GoingOutMode() with CHARGER if-statement commented out does not work

enable_GoingInMode() with checkHeadSensor if-statement commented out does not work!!!

enable_GoingOutMode() with checkHeadSensor if-statement commented out

void DriveForward(uint16_t x){ is weird...

Wait...ALLOW_USELESS_RUNS???

checkHeadSensor is definitely an issue. I have modified the bit relevant to goingOut mode that is reflective of the behavior for goingIn mode.

checkHeadSensor for goingIn mode looks like it has a 1 second check in it, but it really doesn’t. The syntax is wrong and the compiler isn’t catching it for some reason. However, for the goingOut mode, there is a proper 1 second delay, during which the PID feedback dominates the behavior of the robot.

Date: November 1, 2016

Went to check the IMU with an oscilloscope with Andy and he shorted the power distribution board immediately :( Calling it a day. Will try to take the Power Distribution board from...some other robot i guess?

Arduino Due (https://www.arduino.cc/en/Main/ArduinoBoardDue) page says “The board can operate on an external supply of 6 to 20 volts. If supplied with less than 7V, however, the 5V pin may supply less than five volts and the board may be unstable. If using more than 12V, the voltage regulator may overheat and damage the board. The recommended range is 7 to 12 volts.”

I think this could be a source of the issues regarding the PixyCam power, as we supply 5V, which is beneath the recommended range given above.

We are also only using 220uF capacitors, when all of the documentation left by JSP and Vadim indicates that they should be 470uF.

Static memory allocation for the PixyCam data.

Power Distribution Board Review:

Battery 3.6V goes to current sensor, and GND goes to GND.

Date: November 2, 2016

Might need to order more of the Crydom DM0063

Accidentally snipped the wires on Charlie instead of Bravo...oops.

Date: November 3, 2016

I did some more reading on the recommended capacitors to include in the circuit near the voltage regulator here (https://www.pololu.com/docs/0J16), and found that while the minimum recommendation the provide points to a 33 microfarad capacitor with a 35V rating, the bigger the capacitor the better so long as the dimensions of the circuit allow it. This leads me to believe that the 220 microfarad 25V capacitors will be sufficient for our purpose.

Date: November 4, 2016

The maintenance guys are working at my desk, so I am sitting in Andi’s spot for the time being. To do today:

- Recheck the breadboard I made and make sure it is in line with the documentation left by JSP.
  - I am comfortable with the breadboard implementation -- I just need to add some wires which will enable the hookup.
- See if the software can be sufficiently tested on another robot. One of the robots wipes it’s PixyData after driving for a bit, likely to insufficient power. I believe I have already demonstrated that this is not an issue when it is plugged into USB (therefore receiving sufficient power), but I would like to check it again.

Things to check:

1. Voltage across Vin and GND when battery plugged in and system on
2. Voltage across Vin and GND when battery plugged in, system on, and touching charger
3. Voltage across 3.3V and GND when battery plugged in and system on
4. Voltage across 3.3V and GND when battery plugged in, system on, and touching charger
5. Voltage across 5V and GND when battery plugged in and system on
6. Voltage across 5V and GND when battery plugged in, system on, and touching charger
7. Voltage on line going to AnalogA1 on Due -- check that the voltage divider is set up right.

One of my concerns is that the 3.3V which goes to the power distribution board might actually just be whatever the battery voltage is. We should check the range of allowable input voltages on the components on the 3.3V rail.

Date: November 7, 2016

There is a 2V potential across the Crydom mosfet...why? New ones are on the way.

Date: November 9, 2016

Regulators are here and I have been struggling with the breadboard. Initial observation: if all of the systems are plugged in, then the input and output voltages from the 5V regulator are inconsistent. If I unplug the 5V rail on the distribution board then the 3.3V line goes to the battery voltage.

Date: November 10, 2016

More electronics work. I want to swap out the Power Board tomorrow to see if it is an arduino problem or a Power Board problem.

Date: November 11, 2016

I took the power board from Charlie, one of the other non-working robots, and put it on Bravo, which was otherwise operational. Bravo is now working fine.

Bravo run started at approximately 12:05 and ran until around 12:25

- Several intervention was necessary when the charging rod was caught on the charging wire in the corner. This corner is a bad spot to be. The table is uneven which means the robots can bottom out, and the frame holding the spring can hand on the robots’ charging rod.

Working on the power board and modified it a little bit to make the board run on a separate 5v regulator. The results were the same. It turns out one of the 5V regulators I have been working with is toast :(

All robots have power! Still have not deployed a board with the 12V regulator on it.

Started working on Delta and the power is wonky now? I have taken an osilloscope to the regulators and the power going to the Power Distribution Board is not working. Try swapping with another robot.

Date: November 13, 2016

JSP got back to me about the voltage regulator swap-out I have been proposing. Apparently he tried something like this in the past, and came to the conclusion that the 5V regulators are sufficient. He even had a box full of 9V and 12V regulators tucked away in a red box marked “Do Not Use”. Lesson learned.

Goals for the day: I believe I have 3 robots with operational hardware as of now, with only some minor tweaks to get all of them totally operational. During goingOut mode, there is a software issue which causes the robots to pause at approximately 1 second intervals which needs to be resolved, but in the grand scheme of things this is not too big an issue.

- Find cause of goingOut mode pausing behavior: I think I got it. There was a Forward(BASE_SPEED); Delay(1000); command in goingOutModeRoss() which I think might have been causing the issue. Now resolved.
- Tune PID parameters of Alpha: Done - Reduced BASE_SPEED and increased Kd
- Tune goingIn mode direction of Bravo: Done
- Check magnetometer on Bravo: Done - I think it is fine. There was some weird code in the method regarding dumping that I think was causing some issues.

Date: November 14, 2016

- Tune the PID parameters for Echo: Done
- Make a second battery pack so we can run at least two robots at once: Done

Also note that when you want to actually start running trials, you should take the USB cables off! The wheels get caught on the cables of other robots very easily.

Ran the two robots at the same time semi-successfully! Definitely need to increase the size of the capacitive panels on the sides by a pretty good amount.

Realized that I have a homework due tomorrow, not next week, so I have to leave the lab a little early today :(

Date: November 15, 2016

Fixed the capacitive panel on bravo, and got everything running. Checked the capacitive sensor values, and they had hardly changed, which means I might be able to increase the size of the capacitor areas on all of the robots without having to do much tuning. I will say that I think there is a bug in the method which write/reads the capacitive sensor readings to the LCD screen which I hypothesize is losing the last (least significant) bit of the reading.

Working on replacing the left motor on Charlie. Done. Now checking.

Date: November 16, 2016

Something is wrong with the IMU on Charlie? When the sensor is horizontal, the values are stuck between 270-360, but when the sensor is turned vertically, the sensor returns all values. I think I have the IMU on Charlie working now. The PixyCam is also acting weird. When I plug in the Pixy to the USB connect, the entire robot can power up, which does not happen for all of the other robots.

I found that the 5V and 3.3V lines on the Power Distribution Board of Charlie had been crossed (bad), but fixing them (and corrected the RX/TX lines) made the Pixy work. Next is the Force sensors of the gripper.

Date: November 17, 2016

Started looking into why Robot Charlie always thought there was something inside the gripper. It turns out that while the wiring on the robot matches that of the documentation, it does not match any of the other robots. The documentation for the Force Sensitive Resistor Board was wrong, and the 5V and GND wires should be flipped in order for the voltage divider to work with the current implementation of the code.

Broke out the breadboard to start experimenting with the IMU. By itself, the range of values is between 245 degrees and 360 degrees, so that is a bit disappointing. I was able to freeze it and unfreesze it, and now the ranges are totally different.

I can break/reconnect either of the SCL/SDA wires and operation continues. Breaking the ground connection hangs the system, but resetting gets everything going again.

There 5V regulator for the lines going to the PDB is broken - IMU is fine.

- IMU not working? Check the connections and then check the power supply.

Date: November 18, 2016

Took the oscilloscope to the PDB on Charlie and realized that the testing sketch would not be activating the relay supplying power to the IMU. Hooked up the relay control to 5V on the Due and everything is working fine now. The IMU range is still limited to 275-360 degrees, but at least it is communicating.

The IMU only starts returning incorrect values when plugged into the SCL and SDA lines on the PDB.

SDA line alone doesn’t work. SLC line alone doesn’t work.

So now let’s look at what else is connected to the SDA and SLC lines. Maybe something is accidentally grounded?

All of the actual pins on the PDB are good. I checked this by plugging in the SCL and SDA wires from the IMU to each of them with the only other connection being the jumpers going to the SCL/SDA pins on the Due. When I plug in the SCL/SDA wires from the capacitive sensor the IMU hangs, but when I plug in the SCL/SDA wires from the MAG, the IMU still works.

The ground wasn’t connected for the capacitive sensor. So it seems that when any of the boards on the SCL/SDA line hang, all of them will. Specifically, if the GROUND connection is lost, the SDA/SCL communication will hang.

Date: November 28, 2016

Back from exams/holidays! Something on Charlie’s Pixy is weird. The data doesn’t make sense to me. Perhaps it is an issue with syncing? I’m not sure, but I want to table this and work on the other robot for now. When I come back to this, I was to write a script that it Pixy-specific to see what exactly is wrong with the communication protocol.

I took the PDB off of Charlie and put it on Delta, and noticed that the 5V regulator which goes to the PB started heating up just like the original board’s 5V regulator. Is there something wrong with the circuitry on Delta? I put the PDB back on Charlie and it is working fine now. So something is wrong on Delta.

Narrowed it down to the 5V line on PB of Delta. Look here tomorrow.

Date: November 29, 2016

Going to try to figure out what is wrong with the 5V line on the PB of Delta.

PixyCam does not seem to be the source of the issue.

The Hall effect sensor does not seem to be the source of the issue.

The Force Sensitive Resistor Board is also okay.

The Gripper Servo seems to be the issue. When I unplug it, the 5V line returns to 5V.

I wrote a script to test the servo motors and they seem to be working fine on their own. Not sure what is up.

I think everything is working on Delta now. May need to replace the Gripper Servo sometime, but in the meantime see if you can make it work by tweaking the software.

Date: November 30, 2016

I unplugged the gripper servo and everything on Delta works fine now. I e-mailed JSP asking if he has experienced this issue before.

Date: December 1, 2016

Plugged the Gripper Servo into a different set of pins along the 5V regulator line and everything seems to be fine now? Why can’t things start working before I e-mail someone??

Robot Delta has been having an issue with tilting back on the motor mounts when it accelerates. This is because the battery pack is not placed in a very smart place. Additionally, Delta had the 3D printed battery pack on it, which made it weigh approximately 10 grams more than the original design. I replaced the 3D printed version with one of the older packs, and the robot moves much better now. It still rides on the back mounts a bit, but there is less weight on it now and it moves more like the other robots.

Glued the magnetometer to the robot, and now I need to recalibrate the IMU.

After I tuned the IMU on Delta, everything seems to be working fine!

Now onto Charlie. I am thinking there might just be a PID issue going on that I mis-diagnosed as a PixyCam issue. Now to go back and comment out all of those print-statements I put in the Pixy files.

Everything is working! Tomorrow I will work on calibrating the capacitors!

Date: December 2, 2016

Working on getting the capacitive sensors working today. I have to leave early today, but Keith worked out the issues with my building access so I can come in on weekends by myself now!

Plan of attack for capacitors:

First of all, I think there is an issue with the connection between the Due and the Fio, such that the last (least-significant) digit of the write-out is lost. I will test this by writing to serial and to Fio and comparing the output.

Control flow in fio_wireless.ino was a little bit wonky. I interlocked and if-statement with a switch-case statement, but the if-statement conditions were not being enforced. Never run into this issue before. It might be an artifact of the Arduino compiler, or just C++ behavior and I was not using a good practice.

Started calibrating the capacitive sensors.

Date: December 4, 2016

Got sick this weekend – feeling better, but not quite 100%.

Looking at the code in Capacitive Sensor.cpp, the WallDoubleThresh implementation is not sufficient. We need to replace the single WallDoubleThresh variable with two variables WallDoubleThresh1 and WallDoubleThresh2 to store the low and high capacitive thresholds, respectively.

Furthermore, AntThresh is not used anywhere in the code.

Date: December 5, 2016

Tuning capacitors.

Date: December 6, 2016

Sometimes in TurnHeadingRoss the robots will reverse, but not turn. Not sure why this happens, but a reset seems to return the behavior to normal.

Charlie’s IMU is not one-to-one. Not sure what the best solution for this is.

Date: December 7, 2016

Regarding the issue for the robots getting stuck in turn reversal, but not turning. Maybe there is a bug in the capacitive sensor methods which does not call anything? Such that the robot just stays still until it times out?

Working on finding two robot for the demo.

Alpha – Working well enough. Left gripper sensor keeps disconnecting and the one of the Hall Effect sensors has a broken connection.

Quick note: When the robot spins out, it is in the process of switching turn_heading_direction.

Bravo – Works well. Need to tune the capacitive sensors a bit better because of the expanded panel reading false positives.

Charlie – IMU reads 315 twice, one of which is at the IN_DIRECTION point, so half of the time it does not end up in the right direction. Try playing with the IMU a bit. Also need to tune the gripper parameters.

Delta – Works well.

Echo – Working well enough

Spoke with Will about making a resistive touch sensor. Might be worth pursuing.

There are no methods used to handle touching another ant, only walls.

I changed the wiring to the IMU so that it avoids passing near the PDB, and saw an improvement in IMU readings.

Date: December 12, 2016

Weather/stress got me sick, but I’m feeling good enough to be in the lab.

Target for the day is extending the size of the copper panels on Bravo and calibrating them.

Be sure to clean up the lab before you leave for the tour that is coming through tomorrow.

Look for non-conducting materials for the wall material.

Trim up the sides.

So Dr. Goldman had a good insight today. There is an issue with the capacitive sensor in that if two panels are connected via a conducting material, the circuit is essentially shorted such that the reading more or less goes to zero. This is okay for a single material, but if we want to distinguish between two materials touching multiple panels, we need some non-conducting materials in the mix.

Red latex band is okay ~10 drop

Clear Scotch Packaging tape is okay ~10 drop
Duct tape is good ~ 15 drop

Cardboard is bad

Petri dish is okay ~15 drop

Red Brick is good ~35-40 drop

CD material is also good ~ 50 drop

Copper is 712 – 430 = 282

Cooper w/ tape Single Touch = 719 – 625 =

Cooper w/ tape Double Touch = 719 – 427 =

Aluminum w/ tape Single Touch = 711 – 580 = 131
Aluminum w/ tape Double Touch = 724 – 450 = 274

I have found that I can apply a layer of packing tape on the copper and aluminum I can create a sort of composite with unique capacitive readings that do not short when several contacts are made.

Date: December 13, 2016

I added a layer of tape on the aluminum siding of the tunnel, and tuned capacitive parameters of Bravo for both the taped aluminum and the copper panels on the ants. It can sense each of them well.

Next I will increase the size of the panels on all of the other ants.

Finished increasing the panel sizes. Now to tune them.

Also need to find out why the robots reset in exitTunnelMode. I think I got this figured out. There are a lot of cases that need to be implemented. For example, there are some left-side cases in goingOut mode that are not being caught. Whatever the case was, I think I found it. Be sure to implement something similar tomorrow on the right side.

Bravo wires going to the left force resistive sensor are broken.

Date: December 14, 2016

I implemented some new cases that were not being handled in the goingIn/goingOut/goingCharging case that I think were causing some problems. I also changed the default case to reverse for 0.5 seconds, so that at least something happens instead of the previous implementation where Stop() was called. That isn’t a good solution for getting out of a jam.

For Bravo, I moved the power source from the PDB to the Due 3.3V supply, which seems to be better at maintaining the supply when it touches the charging wires.

Check the IMU settings on Delta and extend the top cathode on the charging rod down another couple millimeters.

Found that the I2C connections on Delta were not sound. Reconnected and all issues were resolved.

Tomorrow, let’s work on fitting battery packs onto all of the robots, tuning the IMUs on each robot and making sure all of the wiring is good. From there on, I think there will just be software stuff to tinker with:

Need a way to ensure that the WDT is called in turnheading scenarios.

Perhaps add a check for the IMU WHO_I_AM?

Date: December 15, 2016

Need to tune the PID parameters of Bravo, and figure out why it doesn’t dig well. Also need to tune the IMU a little.

Finished tuning the PID parameters for Bravo. Still need to tune the IMU.

Also need to tune the IMU on Charlie.

Rewrite the implementation of checkWrongDirections so that instead of checking all of the other directions, we only check the direction we are actively moving towards.

Spent all day working on getting battery packs prepared and tuning some PID stuff. Work on getting all robots running together tomorrow.

Date: December 16, 2016

Robots start to seem underpowered at around 3.8V.

goingIn and goingOut are not symmetric in their behavior – working on determining why. Got it sorted out, the checkHeadSensor was modifying the motion a little bit. I thought that I had addressed this issue before, but it seems I hadn’t completely fixed the issue.

I got all 5 robots running today. The ones with the newer battery packs don’t run as well – they are just too heavy. Replace them tomorrow with the older iteration and see if their performance improves. Some wires on the motors broke while I was working on Charlie’s drive train, so that is the first order of business tomorrow.

Afterwards, let’s talk with Bahni about what sort of stuff we need to look at for the reversal/lorentzian implementations.

Date: December 19, 2016

Working on fixing the motor connections on Charlie. I tried a lot of different configurations to address the issue of the robot’s being back-heavy, but did not find a suitable solution. Redesign location of battery pack?

I changed all of the 3D printed battery packs I installed on the robots (Delta and Charlie) back to the insertable kind that was originally used. They are lighter weight, and the reducing of mass on the rear of the robots improves the tracking of the pheromone trail in a significant way.

I because the range of aluminum contacts on the robots is now a single value, but the copper panels still require two ranges, I will just adjust the double contact aluminum values to be sufficiently large values that will never be returned by the capacitive sensor. This is definitely only a temporary solution for the time being, but I think it gets the job done without introducing in sort of glaring potential sources for error.

Temporarily pause? Dr. Goldman and Jeff suggested that another behavior that they have seen is an ant that observes a clog ahead of it and backs up a bit, without totally giving up. It will wait, and then proceed after some given waiting period.

Trying to figure out what is wrong with the IMU:

Added to setup:

dof.setMagScale(dof.M_SCALE_2GS);

dof.setMagODR(dof.M_ODR_125);

Changed in isWantedHeading

float heading=getHeading((float) dof.mx, (float) dof.my);

to:

float heading=getHeading((float) dof.calcMag(dof.mx), (float) dof.calcMag(dof.my));

I have found that the metal screws holding the IMUs in place have a significant effect on the IMU readings after changing the code slightly. This solution worked on robots Alpha and Delta. I discovered better results on Echo, but noted that the hy reading never becomes negative, even after replacing the IMU. I noted that the wiring also has an effect on the outputs, so I need to investigate this a bit more.

Date: December 20, 2016

Trying to figure out why the Echo IMU won’t return a negative hy value – determined I had just been testing with two bad IMUs :/

I think the IMUs just need to be tuned. Create a mapping function?

I wrote a matlab script that may be useful for calibrating IMUs with a bias. I think it works well. Work on porting it to C++ tomorrow.

Date: December 21, 2016

Added in the mapping correction to the getHeading method. It seems to work well on Bravo, which had a pretty bad IMU bias. The bias can drift by around 10 degrees over 30 minutes, so that might be an issue for longer trials. Sometime it seems like a reset can change the IMU bias, but all day today I did not observe that on a robot that ran more or less for ~3 hours, during which it reset many times. I also went through and cleaned up the pickDirection method and verified that everything works with the updated getHeading method. A few things needed tweaking, but for the most part it was all fine. Things to do when I get back:

- Perform the IMU bias correction on all robots.
- Check ellipses? Plot x vs angle to demonstrate deviation in y.
- Clarify what sort of reversal behaviors we want
- Probably need to rework Lorenz implementation?

Date: January 2, 2017

Getting back into things and I noticed this plot in:

C:\Users\vlinevich3\Documents\DiggerDataProcessingProgram

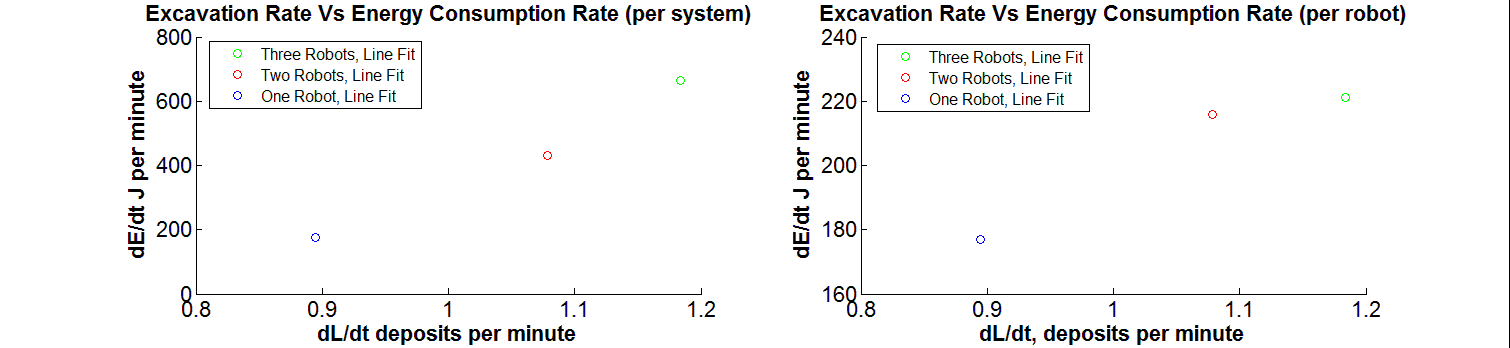
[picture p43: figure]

Super super super speculative, but it looks like the plot on the right might not be increasing linearly?

First thing to do is correct the IMU biases on each of the robots:

Alpha – Done

Bravo – Done

Charlie – Done

Delta – Done

Echo – Done

Date: January 3, 2017

I spoke with Bahni at the end of the day yesterday and if I understood her correctly, there is a behavior that she thinks is dominant in the videos she has reviewed:

Ants are likely to reverse as they go into the tunnel if they bump into another ant which is currently holding something.

In terms of implementing this, Bahni and I think an additional hardware system would be required. At the moment, there is no way for ants to share information with one another, even locally. Bahni suggested an LED might be useful, because we can use the PixyCam on the robots to observe the states of nearby robots without it necessarily being globally networked information.

In the meantime, now that the IMUs have been calibrated, I need to obtain their IN_/OUT_DIRECTION parameters, and work on the methods which allow the robots to give-up and perform the Lorenz trials.

Removed preferGyro functionality from the code.

Changed a recursive call in the dumping method to a do-while loop. This can be modified with a counter in the future to prevent the robots from getting stuck in the dumping state if there is an issue with the cohesive material being stuck in the gripper.

Possible changes for tomorrow:

DUMPING_SWITCH is now longer useful in goingIn mode.

CheckPayload is not necessary in GoingOutModeRoss.

For goingIn method, enable_turnReversalMode(7) redirects the flow of control to exitTunnel, instead of goingOut mode.

Besides these minor changes, I think I understand the code for the useless-run behavior well. Next is the Lorenz runs.

leaveDumpingSite() has bumpDelay() in it…not sure it works.

Is charging always allowed?...this might be what had been causing the robots to restart?

Charging stuff is pretty messy.

Spoke with Will about when Lorenz-evaluations take place. Currently the code only checks after a dumping event takes place, which is not in line with what Will has done. Instead, it might be better to have the Lorenz check in the goingIn portion of the control flow.

Date: January 4, 2017

I think it might be best to move the Lorenz check from the DumpingMode() code to the if(goingIn)-statement in loop() such that it is the first thing that is checked. This is a change that I suggest because the current implementation does not actually begin to exhibit Lorenzian behavior until after the first dig/dump cycle has taken place, during which it is what we would classify as “active”.

If PROBABILITY_DIG statement in evaluates to true within the goingIn if-statement, change the current_target_heading to OUT_DIRECTION, call enable_RestingMode(), and skip the rest of the functionality which sets up a goingIn run.

Before going into the details and testing the code, I want to give a little explanation for what I believe the main issue with the IMUs is and the solution I have come up with. It seems that these IMUs can have a significant bias in them which will affect the sign of their readings. Ideally, the IMU readings will be centered at zero, but in reality we see something like

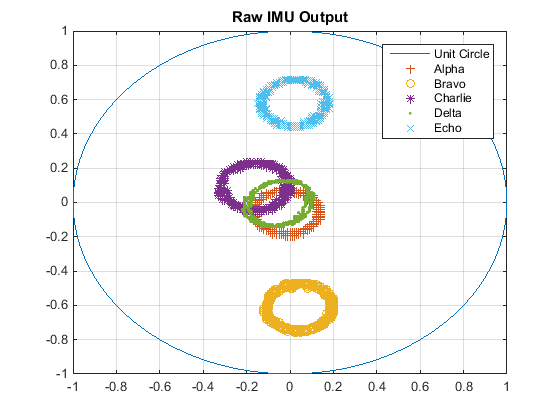
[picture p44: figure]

I have written a matlab script ant-robots/debug/imu/imuCal.m and an accompanying ant-robots/debug/imu/imuCalDisp.m which will print out the parameters necessary for a mapping-technique I have added to the getHeading() function in the due*.ino code. The result of the mapping is not perfect, as there is some ellipsoidal deformations the current mapping cannot correct for, but it is a definite improvement.

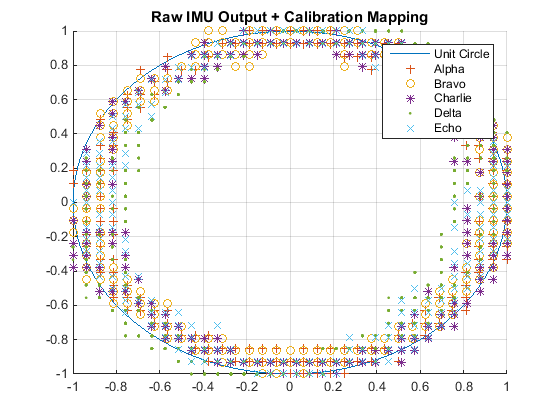
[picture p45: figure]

It does not really matter what the radius of the circle is, or even that it is the same across all robots -- I chose to make the unit circle a standard for the sake of simplicity.

Alpha seems to be running well with the calibrated IMU implementation.

Some quick modifications:

DUMPING_SWITCH is now longer useful in goingIn mode. – Commented out

CheckPayload is not necessary in GoingOutModeRoss. – Commented out

For goingIn method, enable_turnReversalMode(7) redirects the flow of control to exitTunnel, instead of goingOut mode. – Changed to enable_turnReversalMode(3).

Further notes

Dumping mode is a little weird

leaveDumpingSite() has bumpDelay() in it…not sure it works.

Is charging always allowed?...this might be what had been causing the robots to restart?

Charging stuff is pretty messy.

I ended up gutting checkWrongDirections until it was more or less useless. Too much flag/timestamp stuff going on for something that is a rather simple sensor check. A lot of it was folded into some simple stuff tacked on after an isWantedHeading() check. This was motivated by the fact that I wanted to keep tracking the time we were goingIn, even if we needed to handle wrong direction turning and contacts. The way that checkWrongDirections was implemented introduced a break in the control flow that prevented this. Since removing this, the timer should be continuous.

At the moment, the robots will always dump, even if they are performing a useless run. I found a Boolean variable called justSurveying that is not being used for anything in DumpingMode(). This works well. I have renamed justSurveying to uselessRun.

Tomorrow work on getting several robots running with useless runs possible and begin digging into the Lorenz stuff.

What is Lorenz behavior? Right now, if there is a robot which dumps and Lorenz is on, it automatically goes into resting mode. Every resting period, the robot will go digging based on some probability.

Instead, should we roll first to decide if we go dig or go rest?

Date: January 5, 2017

Questions for Will:

- In reversal behavior, does the robot just touch the tunnel and turn around?
  - Will suggested adding a bit of a pause for all cases
- What is Lorenz behavior? Right now, if there is a robot which dumps and Lorenz

is on, it automatically goes into resting mode. Every resting period, the robot will go digging based on some probability.

- Instead, should we roll first to decide if we go dig or go rest?

RandomGenerator.h has some enable_*Mode() stuff in it that should probably be removed.

Need to update software on Fio, as the MasterSlaveProtocol.h file on the Fio was not up to date with that on the Due.

For the time being, there is not a LorenzMode-method. Just a check-loop that can be turned on or off within the goingIn setup. This is sufficient for now, but if we want the behavior to become more complex, such as incorporating charging behavior, then it will probably be smarter to break the Lorenz stuff out into a separate mode.

So I started implementing the Lorenz behavior, and when the robot “wakes up” it would go into goingIn mode and then immediately go into digging mode. I checked the readout from the mag and it was reading the max value. I think I have found the solution, which is a re-FSensor.setup() call. I am guessing this will be necessary for all of the devices on the I2C communication.

Wrote a wakeUp method that takes care of turning the relay back on and re-establishing comms with all of the I2C devices.

The PID on Alpha is a little weird. Trying to figure out if it is a code thing or an Alpha issue.

Code delay issue. The contacts loop can take up to ~500 ms, which is a pretty long time. Trying to incorporate FollowLane into the contact loop. There is a 100 ms delay in there. Maybe we could make it call FollowLane for that period of time?

Date: January 7, 2017

Came in to work on the delay/PID handling. Alpha seems to be working well, but I need to 3D print another motor mount for it. It looks like the current one has been fixed with glue 3 or 4 times already.

I believe I found the part file in

C:\Users\vlinevich3\Desktop\JSP - Ant Robot Gen 2 SolidWork Files\DIGGER\ Motor Mount Block Sideways_Modified.SLDPRT

Going to switch to Robot Charlie – Need to calibrate capacitive sensors.

Date: January 8, 2017

Think I fixed the capacitive sensors on Charlie. Need to add a nut to one of the screws in the gripper and update the software on the Fio.

Updated Fio software on Charlie.

Next I need to update the goingOut method to behavior similar to the new goingIn method.

Should also probably remove the extra cable ribbons that are attached to some of the IMUs.

The ribbons on Charlie have been removed, and I did some work with the wires which I believe was causing some false positive readings from the capacitive sensors. Might need to recalibrate the IMU on Charlie, but it seems to be fine.

Tomorrow begin testing reversal, Lorenz, and reversal/Lorenz tomorrow.

Date: January 9, 2017

- Tune IMU on Charlie…Done
- Update Fio on Charlie…Done
- Tune IMU on Bravo…Done – note that the parameters from last week, literally 7 days ago, were virtually the same.
- Update Fio on Bravo - Done
- Tune IMU on Echo - Done
- Update Fio on Echo – Done
- Bravo in/out directions – Done
- Charlie in/out directions – Done
- Echo in/out directions – Done
- Evaluate Bravo
  - Regular – Done
  - Reversal – Done
  - Lorenz
  - Reversal-Lorenz
- Evaluate Charlie
  - Regular
  - Reversal
  - Lorenz
  - Reversal-Lorenz
- Evaluate Echo
  - Regular
  - Reversal
  - Lorenz
  - Reversal-Lorenz
- Combine them

Today I asked Jeff to show me how to use the webcams in the ceiling to record video. He showed me a few different softwares such as Yawcam and Processing, but both of them have issues supporting two webcams, particularly when they are the same camera with the same name. Ultimately we ended up in MATLAB, which was working well, but would freeze regularly, again due to the fact that the cameras have the same name. I followed the directions found here (http://www.avoiderrors.net/rename-devices-device-manager/) and had to give extra permissions to PHYS32192\vlinevich3 but I removed them after successfully editing both FriendlyName values to “USB_Camera1” and “USB_Camera2”. The Name field values for the webcam object in MATLAB is still unchanged as “USB_Camera”, but they do not hang when I stream video from them.

Ehh, matlab freezing wasn’t resolved by the renaming method given above, but it looks like the VLC media player might be working. I think this is because MATLAB distinguishes them using the Bas reported device description instead of the FreindlyName field, which I cannot change.

We may not need both of the cameras? It seems like the camera closer to the digging surface can see the entire system.

Found that both of the wires going to Bravo’s left FRS are broken. – Fixed

Need to update Lorenz to handle resets in tunnel:

If see green, go to goingIn mode.

If not see green, go to goingOut mode.

I think I found some code that might have been causing the resetting issues in the fio*.ino code. See code associated with CHECK_START and CHECK_END. I commented this out for now. My hypothesis is that there is some accidental flag switching going on here which triggers the reset.

Date: January 10, 2017

I 3D printed a motor mount yesterday that is slightly different than what is currently being used. I think it might be better, so I want to add it to see what happens.

To do today:

- Add new motor mount to Bravo.
  - Seems to increase the balance of the robots substantially, and Bravo digs much better with it. Sent an email to JSP to get his thoughts on the matter, but I may end up printing 4 more for the other robots.
- See if the resetting behavior still occurs. I commented out some Fio code, so upload that to see if it causes any issues – currently on Bravo. Today I only observed resetting when the robot touched the charging wires.
- If the resetting behavior continues, we need to work on a reset check state.
  - To do this, we need to write a method to check how many pixels the green takes up…or use the IMU with a pretty simple direction classifier…probably both, because Lorenz.

I found that I had accidentally included an extraneous FollowLane call in the capacitive sensor check that did not have the proper state conditions applied, which is why ExitTunnel was acting so weird. Added the appropriate state-checks and everything is groovy.

I wrote a method called determineState() which is executed at the very end of setup() which looks at the current heading of the robot as well as the gripper state to guess which state the robot was in prior to being reset. Need to add a green color check for the Lorenz runs. I probably need to make another method specifically for Lorenz mode.

Date: January 11, 2017

Today I need to add a Lorenz-check which is associated with the green color. After that I will evaluate the determineState control flow and begin testing with multiple robots.

I want to pull the Lorenz mode out of the goingInMode state and have it as an intermediary state between goingIn and goingOut.

So there is some stuff in the visionMethods.h file that could use some cleaning up, but I think I got the Lorenz stuff worked out. COTTON and Area7 are not correct, use Areat to see green!

Now I need to write the Lorenz-state method and make the robot go to that after dumping.

Check the various states:

- Regular – Good
- Reversal
  - Facing in empty – done
  - Facing out empty – done
  - Facing in holding – done
  - Facing out holding – done
- Lorenz – Done

It turns out there are several robots with broken motor mounts, so I will need to print more anyway. I am waiting to hear from JSP, but I think I might start using these newer brackets.

Need to make sure the gripper is raised in resting mode. – This isn’t possible, because the gripper is servoed on power that is turned off by the relay in resting mode.

Tune the grippers on all robots so that closed is actually closed.

Echo also keeps wiping the PixyCam memory. Need to add some wire to the lower part of the charging rod. – I think the PixyCam issue on Echo was due to a loose battery wire which caused inconsistent supply voltages, which has been known to wipe the memory of the PixyCam.

Fix the FSR on Charlie. – Done

Tack the motors on Bravo in with hot glue. – Done

Ran 4 robots today with moderate success :D

Will sent me an email with some Lorenz probability stuff, copied below:

2 ants:

0.1036

0.8964

3 ants:

0.0331

0.2161

0.7507

4 ants:

0.0180

0.0856

0.2529

0.6435

5 ants:

0.0118

0.0395

0.1265

0.2532

0.5690

20 time steps with ant velocity at 1 body length per second.

But how long is the tunnel? Do we need to scale for that? I don’t think so, but I want to ask.

I also noticed that a lot of ants will detect a magnetic field from other ants. Do I need to adjust the threshold for the MAG2110asdSDFasdasdfgsdfgASDF?

Date: January 12, 2017

JSP response about new motor bracket:

“Hey Ross:

It's good to hear that the project is going well.

To answer your question, I did try modifying the motor mount to find better balance for the robot.

Be advised, if you use the modified motor mount, you will have to rewrite the PD controller, because the motor position is now different such that it behaves differently. I would expect this to take a week or so.

I would recommend that you use the current version, because if you do use the modified version, you will also have to reinstall the motor on all robots as well. Some robots have motors back from Vadim's days, so they are all glued together to the motor mount. Removing the motors alone will be impossible and they will break.

However, if you are done with other issues that the robot had, it might be worth a try.

Thanks,

JSP”

I am going to print the new brackets. I think the PID stuff will not be a giant issue, so the arduous task is to get the motors out of the old brackets. They are currently printing, and I hope to spend Friday putting them onto the robots.

In the meantime, I want to work on getting data from the SD cards (I am worried that resets might make them wipe the data) and check the MAG3110 readings, because I saw a lot of false positives yesterday in the trials. I think it may just be a matter of increasing the field_threshold value in the MAG3110.h file. – Done, seems like it worked.

I want to run a test with the Lorenz parameters Will sent me yesterday, starting with just 2 robots.

2 ants:

0.1036 – Echo

0.8964 – Bravo

1. All Fio stuff is correct.
2. Verify that the batteries are charged.
3. Verify that gripper is closed appropriately when in closed position.
4. Check IMU parameters.
5. Wipe SD cards and upload them.
6. Check each one individually.
7. After confirming each one. Set them all up. Turn on and hit reset button to ensure that the SD cards start clean.

Test went well for probably ~20 minutes before one of the wires going to the left motor on Echo broke. This makes the power distribution go all wonky and wiped the memory of the PixyCam :/ I don’t intend to fix it since I plan on changing the motors out tomorrow anyway.

Bravo ran well, aside from some screws coming loose. Need a better way to handle that.

Also, how do I handle resets in the data log files?

I need to change one of the charging rod towers at the dumping site.

Date: January 13, 2017

12:55 – started trial with new reset-prevention code

I think I got the resetting behavior figured out. I was missing some stuff in the wakeUp() which is in setup() that takes care of handling the charging sensor. Because of this, after the robots had rested, they did not have the sensors set up to handle the charging rod voltage in an appropriate way.

I ran Bravo from 4.2V down to 3.6V in Reversal-Lorenz while I was working on transferring the old motors on the rest of the robots to the new motor brackets. Motors are now in the brackets, but they need to be mounted back on the robot frames and tacked in place with some glue after verifying that they work.

Date: January 16, 2017

Working on mounting the rest of the brackets today.

Alpha – Done. Need to check camera and PID parameters. Also check the capacitive sensors.

Bravo – Already done.

Charlie – Done

Delta – Done. Need to tune the IMU directions and see why the velocity is low. Bad connections?

Echo – Done. I don’t think the PixyCam is working though.

Next time finish calibration for new brackets and tack motors in place with hot glue.

Date: January 17, 2017

Delta gripper servo is acting weird again, but it seems like I have found a solution? Plugging in a loose wire to the 3.3V line seems to make everything behave…?? Probably means there is some bad solder connections on the PDB itself.

Alpha – Need to check camera and PID parameters. Also check the capacitive sensors. – Done

Delta –I seems to get stuck every once in a while and require a reset. I bet we can determine what is going on by doing a call check to the IMU. I also noticed that the wires going to the Hall effect sensors are about to break. Probably need to resolder these.

Echo – Check the PixyCam is working though….Done

Need to add some sort of magnetic detection for turn heading stuff. We should treat it like a front contact. I added this code into turnheading() and goingout. This seems to do the job.

I added a function that allows the robots to determine if there has been a disruption to their I2C communication. They can perform a quick reset in order to reestablish comms.

After class, work on soldering the Hall effect sensors on Delta and tack the motors of each robot in place with hot glue. Then test the robots behavior with the new mag-sensing front bumper response.

Finished fixing the Hall Effect wires on Delta.

Dug into the code for FollowLaneBackwards() and fixed it up so now the robots can move backwards with PID control centering the pink/green colors from the PixyCam.

Date: January 18, 2017

Work on getting a run with three robots running and tack the motors in place.

3 ants started at 11:09AM – 12:26PM:

0.0331 – Alpha

0.2161 – Bravo – took out for 8 minutes starting at 11:50. PB overheated?

0.7507 – Charlie – started resetting on charger?

For the meeting, this week I:

- Corrected the wakeUp() procedures so that the robots do not reset after they have been in a rest state.
- Printed new motor brackets and mounted them on all of the robots.
- Retuned PID for all robots.
- Tuned the magnetometer on the front of the robots to resolve issues with false-positives caused by nearby robots. Need to work on this a bit more
- Added in a behavior to address the issue of running into granular media when we are not trying to dig, which is treated as if it were a contact on both front panels.
- Fixed some miscellaneous broken wires.
- Wires can shake loose, and hang the I2C communication. As far as I have seen, this is really only an issue for the IMU when we are turning. Regardless, I wrote a method which allows the robots to guess whether or not the I2C communication has hung and perform a quick reset to reestablish communication with the I2C devices.
- Wrote method which allows the robots to follow the pheromone trail backwards.
- Things to do this week:
  - Move charging tower out of the way. Really might need to reconstruct the whole depositing area. We might be able to get away with just putting another board behind the charging wires that is another unique color. If the robots can obscure parts of the board, then we can use PID control to navigate to areas where there aren’t robots.
  - The capacitive sensors need to be recalibrated, because replacing the motor brackets moved some of the wires around that are pretty sensitive to position.
  - Work on adding in a sort of reversal behavior that is probability based like Will’s CA work?
  - The contact handling code still needs to be cleaned up
  - Direction stuff while dumping
    - Probably should add an optional parameter to the tolerance for turning, as seen here (http://stackoverflow.com/questions/3784114/how-to-pass-optional-arguments-to-a-method-in-c).
  - Granular media while turning seems to be causing some trouble
  - Write a initiateVoltageDetector(), similar to initiateChargingDetector in ChargingDetector.h and implement it in
  - Work on tracking the robots

Date: January 19, 2017

Will and Andi were showing me how to record video with OBS. We got the settings all in order, and now I need to figure out a way to identify the robots from each other. A color triangle is what Will thinks is best.

Alpha – Red

Bravo – Orange

Charlie – Yellow

Skip green…

Delta – Blue

Echo – Violet

Date: January 23, 2017

Spent the past week trying to get a tracking matlab code running. I think I have something decent working for a single robot, but I need to test it with multiple robots today. Student Dave has a Youtube channel that covers topics such as the Kalman Filter and the Hungarian Algorithm to track robots that might be useful.

Implemented both algorithms from Jennifer and Student Dave. I think Jennifer’s code is better for what we are hoping to do. The predictive stuff of Student Dave’s approach introduces more errors than it prevents.

Date: January 24, 2017

I like Jennifer’s method of tracking the most. I want to set up a trial with three robots to see how it does. The initial video processing is in stDave.m while the tracking is in testRoss.m.

1. Start recording backgroundz – done
2. Start charging batteries – done
3. Upload appropriate code to the robots – running

0.0331 – Bravo – done

0.2161 – Echo – done

0.7507 – Charlie – done

Currently running and recording! - done

Code stuff:

- Set time to always have a decimal – Done
- Add the word “Frame” to the frame counter – Done

I think I found one of the issues with the robot turning. I must have accidentally copy-and-pasted an incorrect snippet of code which meant the robots no longer tried turning both directions. There is also some inconsistency in the nomenclature for the goingIn/goingOut/exitTunnelMode Boolean values which I had messed up in CapacitiveSensor.cpp.

The robots have started resetting after contacting the charging wires. Has something changed?

I wonder if I need to ground the capacitive sensor to the battery.

3d voxels as the structuring element?

Increase frame rate and increase frame rate

Running median of image

Edge on gaus. Dilate and fill and then bwlabel from there

Date: January 24, 2017

Robots will reset when they touch a resting robot, and then reset on all contacts afterwards.

Trying another setup with an increased frame rate and circular markers. Might be able to use the hough transform?

I tried the edge stuff that Jennifer suggested, which worked well at the beginning of the trials, but edges would appear in the granular material after digging. I tried doing a sort of background update which would exclude the regions in which the robots were detected, but the detection regions would not cover the entire robot and then the robot bodies would work their ways into the average.

Dr. Goldman has suggested just streaming the video to matlab and then getting the XY coordinates of the robots and saving those data at a high frame rate and writing the frames out to another file for actual video output.

Look at HSV and talk to Bahni about QR code.

Reversal when not see pink, front contact, and facing in, and going in for more than x seconds?

Date: January 26, 2017

Bahni is using HSV with a kmeans classifier to ID painted ants. Might be able to use this with the construction paper she showed me. Also, never record at 10 fps. Takes way too long to process.

So it took 26 minutes to read the images and find the centroids as I went.

Just reading the images in to f_bw as a grayscale image takes 2.7877 minutes

Just reading the images in to f_bw as a red-band image takes 2.6207 minutes

Matlab’s imfindcircles consistently takes ~0.1sec per frame.

Initialize

Read in frames to grayscale array

Date: January 27, 2017

Regarding the resets on contacts, maybe we need to add in:

pinMode(irqpin, INPUT);

Turn reversal based on a probability ratio for how long they have been going in evaluated at a contact

(The amount of time they have been going in)/(the time at which they give up) is the probability that they will turn around.

Heatmap with imagesc() command

I am happy with the Hough transform method with the white circles. The tracking has not skipped a frame once, which means Jennifer’s tracking algorithm works very well.

Might want to look at ProcessData.m in Documents/MATLAB/ folder to see how to extract the data from the SIM cards.

Will showed me how to use the fire colormap, and I made this:

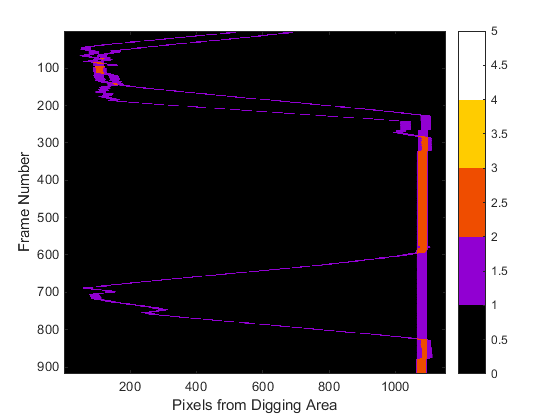
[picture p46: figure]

Going to leave to work on all of the homework I have been putting off :/

Bahni stopped by and we spoke about what we want to test:

15 minute trials with 2, 3 and 4 robots

Track them and make the space-time diagrams along with a contact plot.

Also need to fix the gripper on Charlie.

Date: January 30, 2017

From “Swarm robotics: a review from the swarm engineering persepctive” Pg30

“Group size regulation is the collective capability of creating or selecting a group of a desired size. This can be useful for many reasons. For example, Lerman and Galstyan (2002) showed how an excessive number of robots can reduce the performance of a system, and demonstrated for different behaviors that it is possible to identify a group size that maximizes the performance of the swarm

Melhuish et al. (1999a) used behavior inspired by fireflies to achieve the formation of groups of the desired size. Each robot can emit, at a random time, a signal. The robots then count the number of signals received over a period. The obtained number can be used by the robots to estimate the size of the group and thus to create groups of the desired size. In a related work, Brambilla et al. (2009) improved the original behavior by introducing a more strict signaling order. With this improvement the authors were able to obtain a more robust and reliable estimate of the size of the group.

Pinciroli et al. (2009, 2010) studied a collective behavior able to form groups of robots of the desired size. The swarm is composed of flying robots and terrestrial moving robots. The ground robots perform aggregation under the flying robots. The probabilities used by them to join or leave a group are communicated by the flying robots according to the size of the group itself. With this simple mechanism the robots are able to form groups of various sizes.”

If you have a population of ants which emit some sort of signal based on the last time that they went in, then each ant could poll those around them. If the ant poll determines that a number of them have not dug in some threshold, they have a probability of going to dig. This allows for a workforce selection to emerge like the group size selection for the fireflies.

Get the robot hand printing. - Done

Start the trials suggested by Bahni – First I will set up a trial with two robots which are in the active and non-reversal state. This will be bad, but I do not expect it to clog. Starts at 1:38, run for 15 minutes.

The robots started resetting frequently during this run. Not sure why I tried recreating the issue with a single robot, thinking it was a Fio issue when the reset it hit, but I couldn’t reproduce the issue. Probably a capacitive sensor issue? I am doing a run with the reset wires unplugged, which seems to solve the problem? Maybe?

I am going to leave the reset wire on the Due unplugged and remove the reset calling behavior on the Fios, so that all the reset button does is wipe the SD cards.

Second trial started. Stop at 3:05

Go get the gripper part and come back to set up another trial with 2 robots in nonreversal mode. Chip away the support material while it runs.

Firefly algorithm reading.

Reading notes for “Mathematical Model of Forging in a Group of Robots” by Lerman and Galstyan 2002: Seems very similar to what Will has found in the simulations.

Date: January 31, 2017

Plan for the day:

- Run 3 robots for 15 minutes in active-no reversal
- Run 4 robots for 15 minutes in active no reversal

Need to charge the batteries - done

Need to get 2 more SD cards - done

Need to cut out 2 more circles – done

Need to update Fio code on 2 additional robots and unplug the reset wire from the Due boards – done

3 running at ~10:00

Work on writing a script to read in the all of the .txt files from the SD card

After the presentation, go print out the papers for the Digital controls homework.

Delta keeps wiping the memory on the PixyCam, which is indicative of a power supply issue. I put the Pixy power on the regulated 5v line of the Due, only for Delta.

Got some good matlab code written today. I noticed that while I did not observe any resets by the Dues, I can see several resets in the SD card memory, meaning the Fios were resetting themselves. All in all, I think the power boards are not working well. Tomorrow show Bahni how you can power a Due through the Pixy…

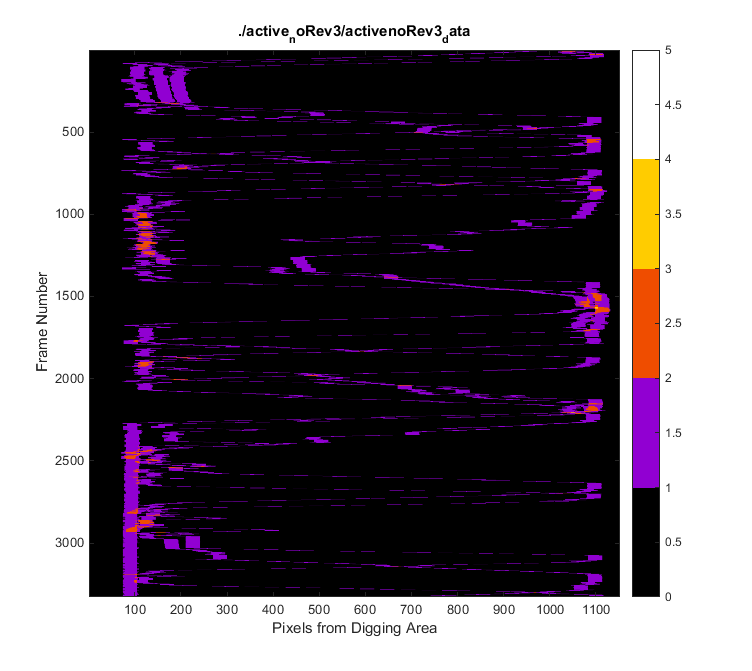
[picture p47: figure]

Date: February 1, 2017

- Figure out what is going on with Echo - done
- I want to see what happens when we power the fio off of the Due 3.3v line and not the Lipo battery connection.
- Run 4 robots for 15 minutes in active no reversal

Separate out panels and types

Number of digs

Email JSP and Bahni about circuit diagram

- Capacitors

Fix diagrams with contacts

Order more batteries

Date: February 3, 2017

Spent yesterday working on school stuff, but ended up spending the morning on it because the lab machine deleted some *.m files

Going to work on parsing the contact data today and hopefully run a five robot experiment if I can get the robot gripper swapped out.

Pull the fioWrites out of the action-causing switch cases. This is going to result in double/triple/quadruple counting – done.

Working on consolidating Fio functionality into the Due. Need to test the SD stuff.

Date: February 5, 2017

Something is wrong with Alpha’s current sensor and Bravo’s as well. I think it has to do with the initialization of the pin that is reading the values. In the activeNoRev4/Bravo/CURRLOG.txt you can see that after some resets the sensor is being read properly, but not always. – I believe I have fixed the current and voltmeter initialization issues on the Fio.

I am playing around with the idea of removing the Fio altogether. I want to do a single robot run with the Fio unplugged.

I unplugged the Fio on Echo and started it with some old batteries at ~2:50. I want to let it run until it fails in some way. In the past, Echo has been wiping the Pixy setting frequently. Wiped memory at 3:45 with battV at 3.7

It might be possible for the robots to be able to tell which part of the other robots they are touching. Because the aluminum is covered in tape, we might be able to add uncovered aluminum to one side of the robots so that they can distinguish which side of the robots they are touching.

The gripper on Charlie is fixed. Probably need to replace one of the motors on Charlie.

Tomorrow let’s hook up Echo’s Pixy to the 5V pin on the Arduino and see if the memory ever wipes.

Date: February 6, 2017

I have successfully ported the serLCD library used by the Fio to communicate to the LCD screen so that it can work on the Due, which does not support the SoftwareSerial methods which serLCD relies on. I have called this new library hardSerLCD, as it uses the hardwareserial ports on the Due to communicate via any of the TX ports. It was easy, but I haven’t found anything close to this online and it might be worth publishing.

So the maximum supply current on the 5V regulator is between 0.74 and 0.84 amps, but the stall current of a single servo is 1.2 amps, so right there we already have an issue. Looking for a VR with a higher current output capacity.

http://www.digikey.com/product-detail/en/texas-instruments/LM338T-NOPB/LM338T-NOPB-ND/212669

http://hitecrcd.com/products/servos/sport-servos/digital-sport-servos/hs-5485hb-standard-karbonite-digital-servo/product

Date: February 7, 2017

I have been reading a lot of papers lately, and need to take some time to organize everything. Today my tasks are to read and check Echo to make sure everything on board survived the power tests I performed yesterday. I also want to write another email to JSP to prompt a response.

Reading “On foraging strategies for large-scale multi-robot systems” and found something interesting:

“What is unexpected, however, is that even large D values (40m is large, relative to the size of the arena) can have a marked interference-reducing effect. For large D values, several robots will still attempt to transport a puck toward the home region, but they do not remain in the crowded region as long as homogeneous robots. We believe that this because, as can be seen in Figure 1, odometric drift forces some robots to yield, having believed to have passed outside the radius D disk. The drift is exacerbated around the crowded home region because much time is spent turning in place. In physical robots, such turns often distort the odometric frame of reference negatively, which is faithfully reproduced in our simulation. This factor appears to be sufficient to break deadlocks within groups of otherwise greedy robots crowding the home region and areas surrounding it.”

It might be worthwhile to talk to Dr. Shell about the software he used in this paper.

Reading “Cost, Precision, and Task Structure in Aggression-based arbitration for minimalist robot cooperation”:

“Taxonomy of spatial conflict resolution models

We propose a taxonomy of conflict resolution models with the following axes:

• Dynamic vs. static: An arbitration method is static if and only if it does not employ information about a particular encounter to resolve that conflict.

• Deterministic (DET) vs. Probabilistic (PROB): A method is deterministic if and only if, given the same scenario, the resource is always awarded to the same agent.

• High (HOA) vs. Low outcome accuracy (LOA): The former has higher probability of selecting the rational winner. The robot with the greatest local investment should gain the resource in rational interactions.

• Costly (HIGHCOST) vs. cheap (LOWCOST): Time, energy and other resources may be involved in an arbitration mechanism. Their utility depends on the comparative saving and/or trade-off of these costs”

Reading “Collective Energy Distribution: Maintaining the Energy Balance in Distributed Autonomous Robots using Trophallaxis”:

Interesting energy-based trophallaxis concept. What if instead of energy, the robots trade workload based on the energy they have left?

Reading “Collecting Behavior of Interacting Robots with Virtual Pheromone” touches lightly on congestion issues. Take a look at the references.

Reading “Communication of behavioral state in multi-agent retrieval tasks” good references for ants

Reading “Temporal Heterogeneity and the value of slowness in robotic systems” – A little weird, but good sources.

Temporal heterogeneity and the value of laziness in robotic systems

I found two theses which I should read at some point:

“Interaction and Intelligent Behavior” by Maja J Mataric

“Evaluating the dynamics of agent-environment interaction” by Dani Goldberg

Reading “Emergent bucket brigading – a simple mechanism for improving performance in multi-robot constrained-space foraging tasks”: Good coverage of the effects of interference.

Reading “Go ahead, make my day: Robot conflict resolution by aggressive competition”: I like the way they present the population-performance tradeoff graph, and the language they use is very easy to understand.

Reading “Ganging up: Team-based aggression expands the population/performance envelope in a multi-robot system” – This Vaughan guy is a goldmine.

Echo seems to be fine! I found some more evidence that there is a power distribution issue on the robots. I can make them stall by placing a finger in front of them and touching the base of the pitch servo. This causes them to stall, drawing high current. If the Pixy is on the PDB and not the Due, the robot will reset. The maximum load current is 3A, which is not high enough.

Alpha and Delta have PB issues. Try moving the Pixy 5V line on Delta to the Due 5V pin. Done.

Date: February 8, 2017

Found “A study of territoriality: the Rolle of critical mass in adaptive task division”

https://www.pololu.com/product/2866

https://learn.adafruit.com/multi-cell-lipo-charging?view=all

http://www.linear.com/parametric/Step-Up_(Boost)_Regulators#!1646_Boost|Buck-Boost!1032_<=2.9!1033_>=4.3!1034_>=5!1035_17.2:60!1107_6:60!vinmin_2.9!vinmax_4.3!vout_5!iout_6!vout2_!iout2_!vout3_!iout3_

https://www.reddit.com/r/AskElectronics/comments/2mp901/high_current_37v_to_5v_boost_converter_12a/

http://uk.rs-online.com/web/p/buck-boost-switching-regulators/5455001/

http://uk.rs-online.com/web/p/buck-boost-switching-regulators/7798981/

http://uk.rs-online.com/web/p/buck-boost-switching-regulators/5454991/

https://store.ti.com/LM2577T-ADJ/NOPB.aspx

http://uk.rs-online.com/web/p/dc-dc-wandler/8225957/

Date: February 9, 2017

Trying to figure out how to manage the lack of power in an appropriate way. I think I got a good thing worked out. The relay controls the 5V line to the motors and servos now, and all other power is drawn from the Due.

The motors and servos still compete for power, but now at least they won’t reset anything (I think). Need to remember to account for this competition when writing software.

Date: February 10, 2017

Bahni sent me some references for better voltage regulators.

The LT1038 (http://cds.linear.com/docs/en/datasheet/1038fa.pdf) would be good, but they are rare and expensive :/

For the LM338, the range of possible input/output voltage differentials is between -0.3 and 40V. For us, Vin=3.7-4.2V and Vout=5V, so the range of voltage differentials we will expect is -1.3V to -0.8V. Reading forums online suggests that Vin needs to be at least Vout+3V in order to get consistent behavior.

With the 3.3V stuff coming off of the Due, the Alpha can still move along quite well as low as 3.6V.

Next step is to move non-servo/motor 5V stuff to Due as well.

While the voltage regulators might be maxed out, it would be nice to get a relay that is not red-lining all the time:

http://www.digikey.com/product-detail/en/crydom-co/CMX60D5/CC1667-ND/751911

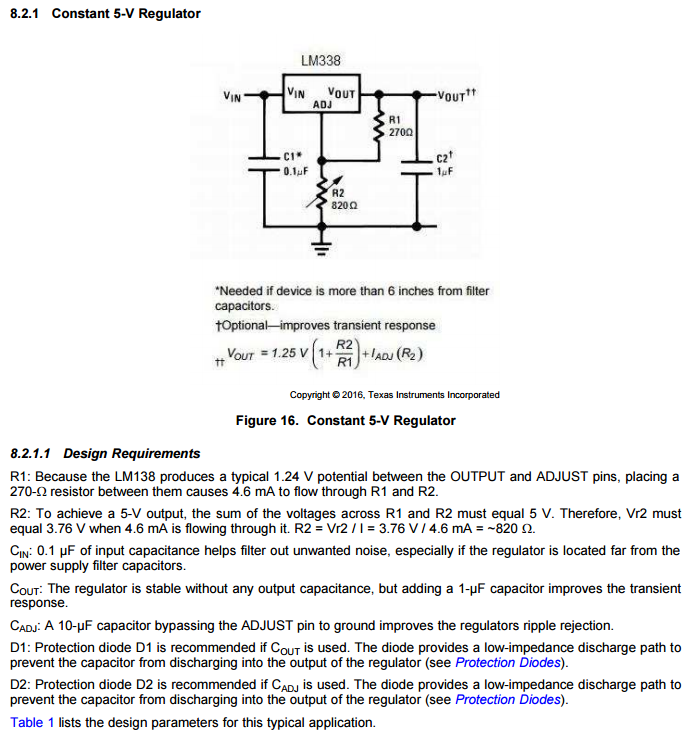
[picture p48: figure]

Dr. Goldman would like for me to write up a paragraph comparing what research has been done in the past in robotic systems to what I am currently working on in CRABLAB.

Date: February 13, 2017

Literature review I sent to Dr. Goldman:

I have not actually seen the paper that you have been working on, but based on the conversations I have had with members of the lab, the objective of the research is to develop an understanding of the effect of workload distribution on overall system productivity. This research has been performed by intentionally manipulating and enforcing the distribution of labor among a population of simulated or robotic agents, which I have not found in previous literature.

This topic straddles two subjects of research in collective robotic systems: task allocation and interference. With regards to task allocation, a bulk of the literature focuses on centralized control and market-based task distribution, though some decentralized ant-emulating methods have been researched. Perhaps the most relevant work is that by Krieger et al. 2000 and Yang et al. 2009. Both utilized activation threshold equations which enabled robots to be determine behaviors based on various local inputs. However, these studies investigated the best way for systems to manage energy consumption in situations where energy must be expended to forage and find more energy sources. These studies focused on local algorithms to manage energy consumption, while the research you intend to present is not concerned with the robotic control algorithm. Your research takes a step back, and identifies the workload distribution that swarming robotic control algorithms such as those by Krieger and Yang should attempt to emulate when engaged in high-interference transportation tasks.

Physical interference in robot-dense systems has been explored by researchers such as Lerman and Galstyan 2002, who present data that I find remarkably similar to data I have seen presented in our lab for active systems. Many methods have been employed to mitigate interference, such as workspace partitioning, or reduce interference cost, such as Vaughan’s aggression interactions. Interference management has not been handled by intentionally modulating workload distribution. The agents in other interference-management papers perform varying tasks with equal engagement; the agents in Lorenz systems all perform the same task with varying rates of engagement.

Quick citations:

Title: Swarm robots task allocation based on response threshold model

Author: Yang Zhou and Tian 2009

Title: Emergent bucket brigading: a simple mechanism for improving performance in multi-robot constrained space foraging tasks

Author: Ostergaard et al 2001

Title: Mathematical Modeling of Foraging in a Group of Robots

Author: Lerman and Galstyan 2002

Title: Interference as a tool for designing and evaluating multi-robot controllers

Author: Goldberg and Mataric 1997

Title: Ant-like task allocation and recruitment in cooperative robots

Author: Krieger et al. 2000

I spent a majority of the weekend working on several digital controls problems which turns out were impossible, so I didn’t get much research related work done. I have a perfboard populated with all of the components to replace the PDB/Fio. I want to tack everything in place and then get the SD card reader wired up first. Test that everything concerning the SD card is good and then solder the rest of the stuff. Aim is to have a new PDB prototype by the end of the day.

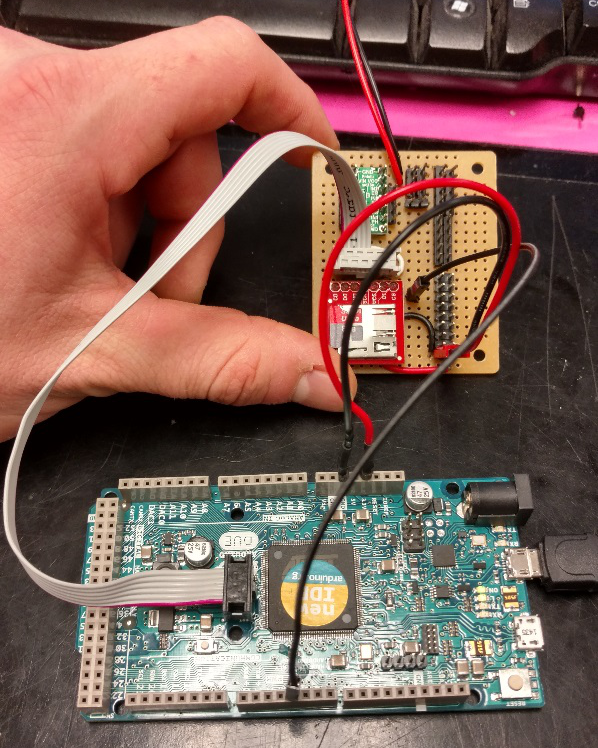
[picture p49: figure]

All soldered up! Going to implement tomorrow :D

Date: February 15, 2017

Wiring took a VERY long time, but I got it working this morning. SD card is not hooked up because I will have to remove the upper part of the robot frame from the bottom to get access to the SPI pins. I am going to let Alpha run down a full set of batteries to see what happens to it. The trial started at 12:00 and by 12:10 I think it has excavated at a rate faster than normal. Stopped at 12:40 when comms acted weird. I2C connection bad? Voltage afterwards was 4.0V

Thinking through how to write various things to the SD card:

- At the start of each state, write the state to STATELOG.TXT
- For contact handling states, write the type of contact to CONLOG.TXT
- Keep a global time variable, and in each state method write to CURRLOG.TXT, VOLTLOG.TXT, and POWERLOG.TXT

Date: February 17, 2017

Two big exams next week with homework as well, so I haven’t been able to get much lab stuff done. I think that Alpha has a bad current sensor.

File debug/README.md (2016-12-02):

# Auxillary Debugging Code

Sometimes I have found the need to debug a single system at a time. The code for doing so is here.

Initial Author: Ross Warkentin  
Email: ross.warkentin@gmail.com

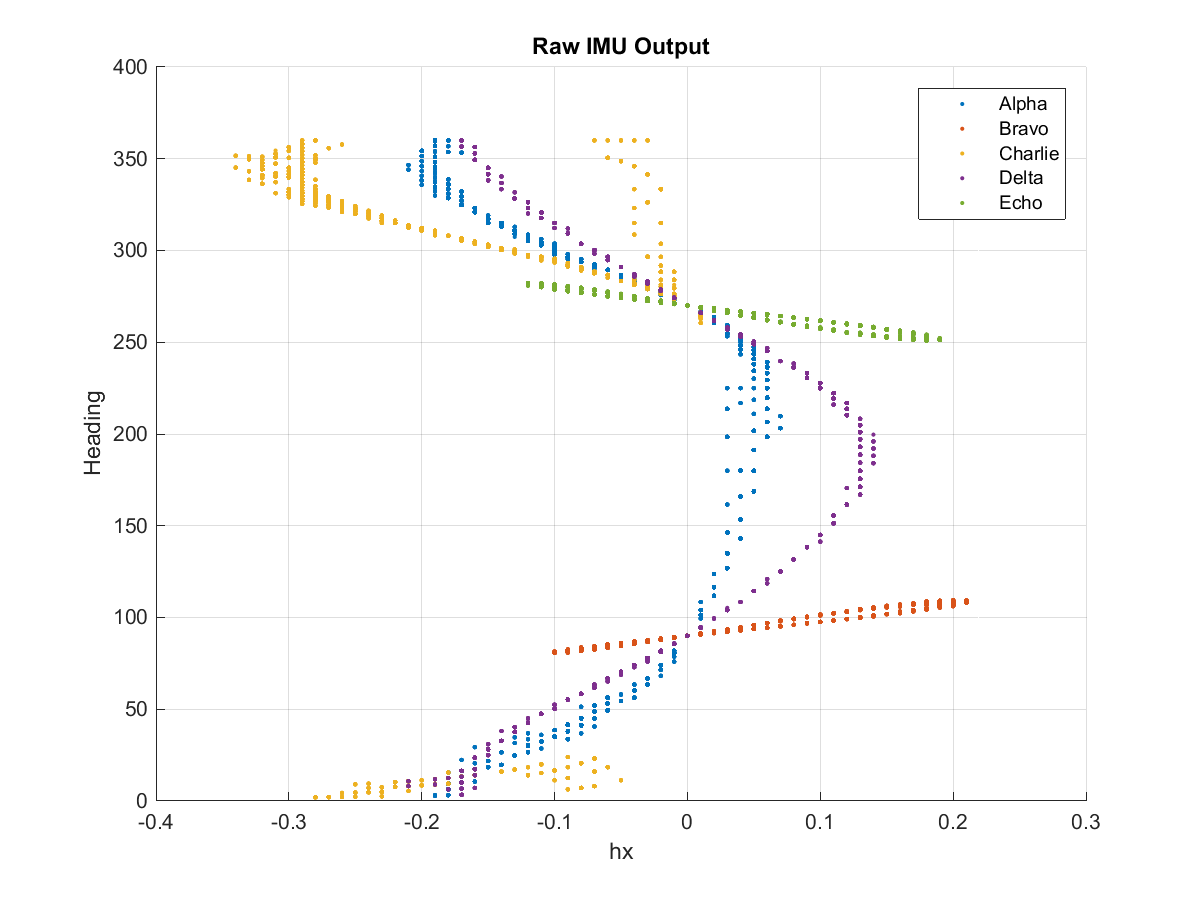
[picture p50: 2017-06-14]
debug/imu/rawHeadingOutput.png

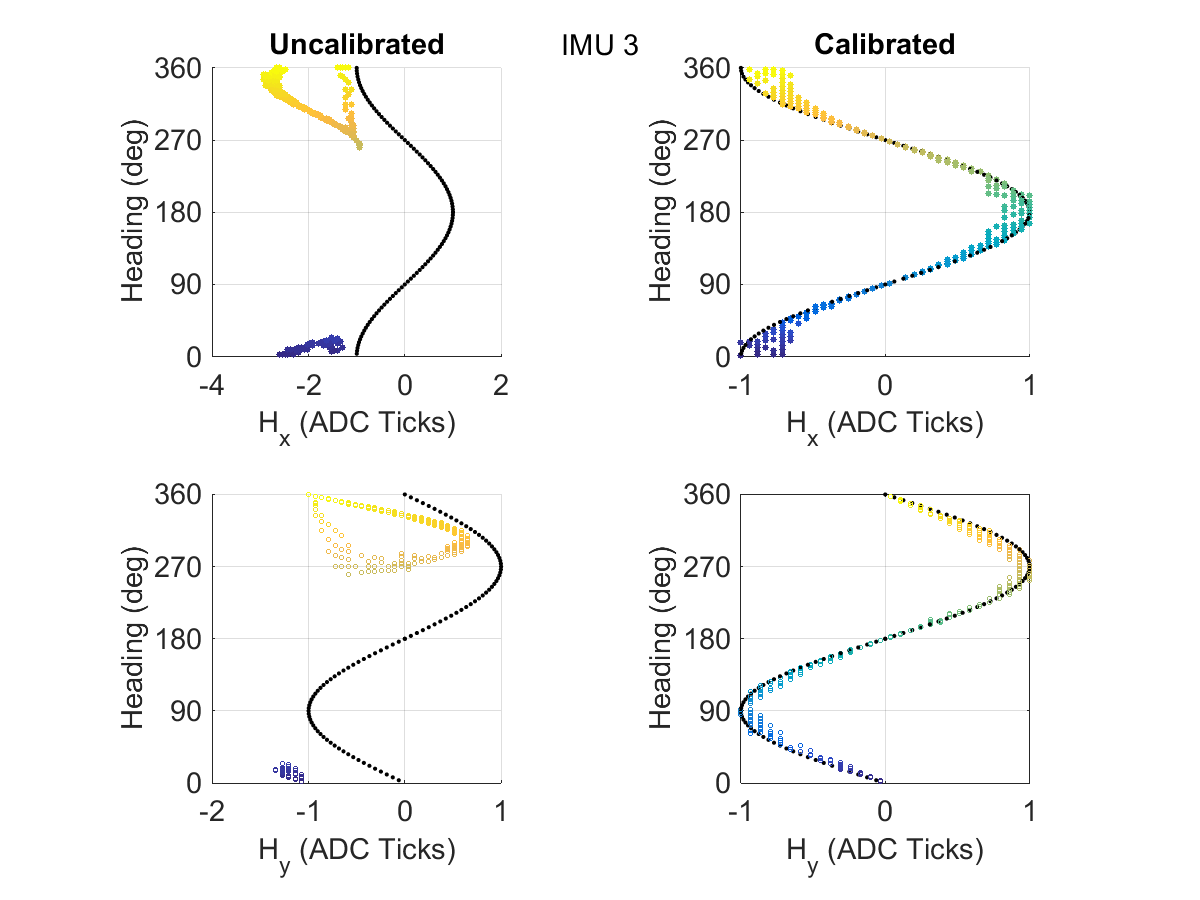
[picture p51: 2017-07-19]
debug/imu/figc.png

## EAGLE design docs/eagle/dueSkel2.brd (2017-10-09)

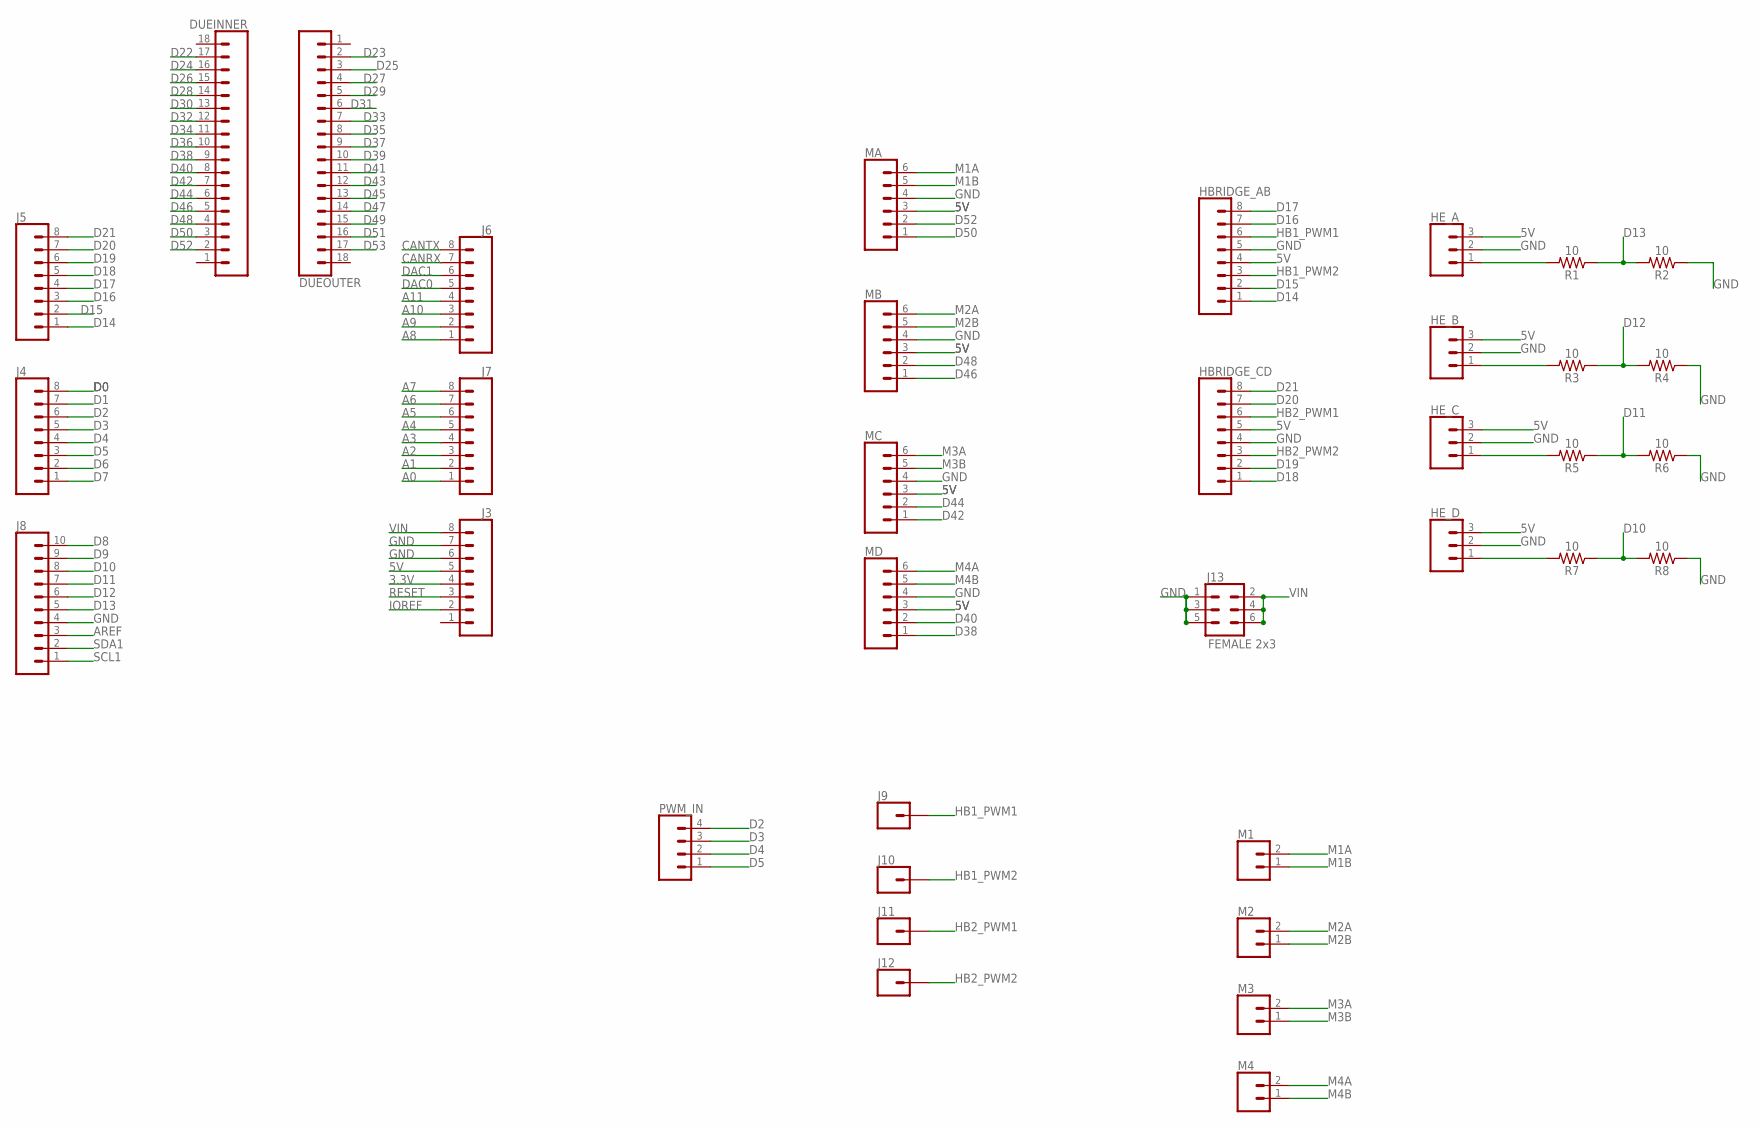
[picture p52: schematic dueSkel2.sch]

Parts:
DUEINNER: CONN_18; 1X18
DUEOUTER: CONN_18; 1X18
HBRIDGE_AB: CONN_08"; 1X08
HBRIDGE_CD: CONN_08"; 1X08
HE_A: CONN_03; 1X03
HE_B: CONN_03; 1X03
HE_C: CONN_03; 1X03
HE_D: CONN_03; 1X03
J3, J4, J5, J6, J7: CONN_08"; 1X08
J8: CONN_10"; 1X10
J9, J10, J11, J12: CONN_01; 1X01
J13: FEMALE 2x3; 2X3
M1, M2, M3, M4: CONN_02; 1X02
MA: CONN_06SILK_FEMALE_PTH; 1X06
MB: CONN_06SILK_FEMALE_PTH; 1X06
MC: CONN_06SILK_FEMALE_PTH; 1X06
MD: CONN_06SILK_FEMALE_PTH; 1X06
PWM_IN: CONN_04; 1X04
R1, R2, R3, R4, R5, R6, R7, R8: 10; AXIAL-0.3

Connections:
3.3V: J3.4
5V: HBRIDGE_AB.4, HBRIDGE_CD.5, HE_A.3, HE_B.3, HE_C.3, HE_D.3, J3.5, MA.3, MB.3, MC.3, MD.3
A0: J7.1
A1: J7.2
A2: J7.3
A3: J7.4
A4: J7.5
A5: J7.6
A6: J7.7
A7: J7.8
A8: J6.1
A9: J6.2
A10: J6.3
A11: J6.4
AREF: J8.3
CANRX: J6.7
CANTX: J6.8
D0: J4.8
D1: J4.7
D2: J4.6, PWM_IN.4
D3: J4.5, PWM_IN.3
D4: J4.4, PWM_IN.2
D5: J4.3, PWM_IN.1
D6: J4.2
D7: J4.1
D8: J8.10
D9: J8.9
D10: J8.8, R7.P$1 (1), R8.P$2 (2)
D11: J8.7, R5.P$1 (1), R6.P$2 (2)
D12: J8.6, R3.P$1 (1), R4.P$2 (2)
D13: J8.5, R1.P$1 (1), R2.P$2 (2)
D14: HBRIDGE_AB.1, J5.1
D15: HBRIDGE_AB.2, J5.2
D16: HBRIDGE_AB.7, J5.3
D17: HBRIDGE_AB.8, J5.4
D18: HBRIDGE_CD.1, J5.5
D19: HBRIDGE_CD.2, J5.6
D20: HBRIDGE_CD.7, J5.7
D21: HBRIDGE_CD.8, J5.8
D22: DUEINNER.17
D23: DUEOUTER.2
D24: DUEINNER.16
D25: DUEOUTER.3
D26: DUEINNER.15
D27: DUEOUTER.4
D28: DUEINNER.14
D29: DUEOUTER.5
D30: DUEINNER.13
D31: DUEOUTER.6
D32: DUEINNER.12
D33: DUEOUTER.7
D34: DUEINNER.11
D35: DUEOUTER.8
D36: DUEINNER.10
D37: DUEOUTER.9
D38: DUEINNER.9, MD.1
D39: DUEOUTER.10
D40: DUEINNER.8, MD.2
D41: DUEOUTER.11
D42: DUEINNER.7, MC.1
D43: DUEOUTER.12
D44: DUEINNER.6, MC.2
D45: DUEOUTER.13
D46: DUEINNER.5, MB.1
D47: DUEOUTER.14
D48: DUEINNER.4, MB.2
D49: DUEOUTER.15
D50: DUEINNER.3, MA.1
D51: DUEOUTER.16
D52: DUEINNER.2, MA.2
D53: DUEOUTER.17
DAC0: J6.5
DAC1: J6.6
GND: HBRIDGE_AB.5, HBRIDGE_CD.4, HE_A.2, HE_B.2, HE_C.2, HE_D.2, J3.6, J3.7, J8.4, J13.1, J13.3, J13.5, MA.4, MB.4, MC.4, MD.4, R2.P$1 (1), R4.P$1 (1), R6.P$1 (1), R8.P$1 (1)
HB1_PWM1: HBRIDGE_AB.6, J9.1
HB1_PWM2: HBRIDGE_AB.3, J10.1
HB2_PWM1: HBRIDGE_CD.6, J11.1
HB2_PWM2: HBRIDGE_CD.3, J12.1
IOREF: J3.2
M1A: M1.2, MA.6
M1B: M1.1, MA.5
M2A: M2.2, MB.6
M2B: M2.1, MB.5
M3A: M3.2, MC.6
M3B: M3.1, MC.5
M4A: M4.2, MD.6
M4B: M4.1, MD.5
unnamed: HE_A.1, R1.P$2 (2)
unnamed: HE_B.1, R3.P$2 (2)
unnamed: HE_C.1, R5.P$2 (2)
unnamed: HE_D.1, R7.P$2 (2)
RESET: J3.3
SCL1: J8.1
SDA1: J8.2
VIN: J3.8, J13.2, J13.4, J13.6

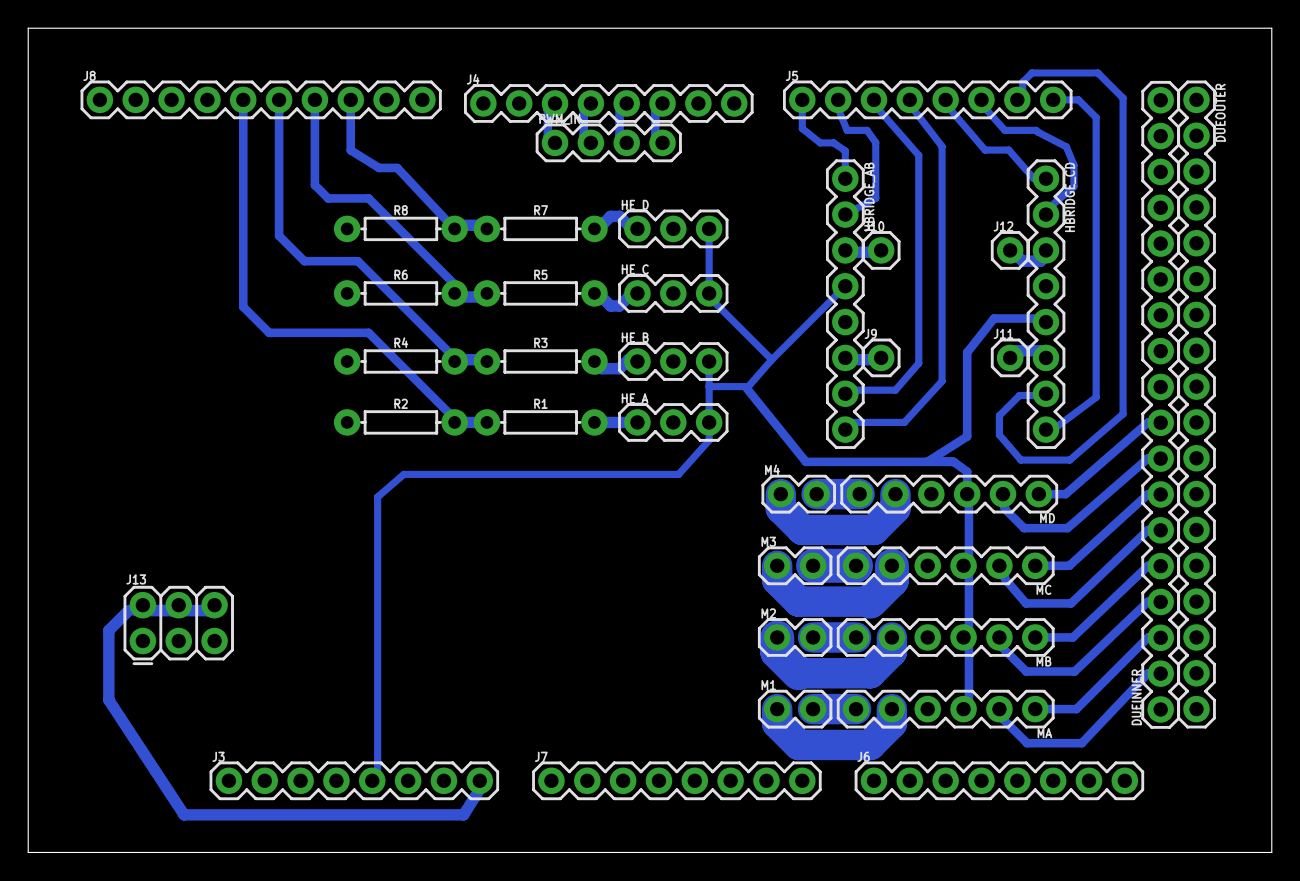
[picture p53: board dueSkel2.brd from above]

Board: 2 copper layers, 88.1 x 58.4 mm, 36 parts (0 on the bottom side), 43 nets.

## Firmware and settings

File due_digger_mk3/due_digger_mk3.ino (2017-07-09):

/**

Author : Vadim Linevich
email  : vadim.linevich@gmail.com

Modified by : Jungsoo Park
email : ryanryan0906@hotmail.com
Last Modified Date: 05/26/2016

Modified by : Ross Warkentin
email: ross.warkentin@gmail.com
Last Modified Date: 07/08/2017

Property of CRABLAB, Georgia Institute of Technology, School of Physics
[2013]-[2014]

This is the main program, written in embedded C++, to be compiled and uploaded
to Arduino family MCU's using ARDUINO IDE (works with v1.5.7)

11/13/2014: the code is specific to Arduino Due

//WATCHDOG RESET IS ENABLED
//read this forum http://forum.arduino.cc/index.php?topic=314647.0

*/

#define FIO_LINK 1

// // ********** BEGIN {SET BEHAVIOR} **********
// //--comment things out if unwanted 
// //lorenz stuff
// #define PROBABILITY_DIG 0 //0 for active, 1 for lorenz
// #define RESTING_TIME 3000// number of seconds before rerolling probabilty in lorenz mode -- was originally 20000
// int lorenzProb = 50;

// //useless run stuff turn back if it did not reach the face
// #define ALLOW_USELESS_RUNS 0 // 1 is allow
// #define USELESS_RUN_THRESH 75000 //used to be 75000 

// //dont worry about this stuff
// #define ALLOW_CHARGING_ON_REST 0
// #define ALLOW_POWER_SAVINGS 0
// //VADIM. FIND A TIMER FROM A PREVIOUS CODE> THIS WAS BROKEN 
// #define BACKWARDS_KICK_TIME 1000   //every so often the robot will drive back for this many seconds. needed for avoiding getting stuck 
// //run trhesh: 40s too short, 120s too long
// // **********  END   {SET BEHAVIOR} ---------

// 2 ants: P1=11, P2=89
// 3 ants: P1=4, P2=21, P3=75
// 4 ants: P1=1.80,  P2=8.56, P3=25.29, P4=64.35


// #define MANUAL_ON 1
// ********** BEGIN {LIBRARY IMPORT} **********
/* note: included libraries with "" must be in the same folder with .ino sketch, while external <> libraries must be in the arduino library folder (either documents>arduino or program files>arduino */
// #include "RobotSelector.h" //load appropriate robot specific definitions and constants 
#include "MotorBoard.h"   //loads a custom library to set up drive motors
//power relay, switches, drive methods, vision methods have def.h files
#include "DiggerArm.h"     //loads a custom library to provide easy arm control command
#include "CurrentSensor.h" //loads a custom library to read data from current sensors
//#include "AntComm.h"       //loads a custom library to set up a wireless communication (Xbee Series 2 Radio)
#include "GripperSensor.h" //loads a custom library to set up a reflective gripper sensor#include <Wire.h>
#include <Wire.h>          //loads external arduino library to set up I2C communication protocol. Used to talk to Pixy camera
// #include <PixyI2C.h>       //loads external arduino library to set up CM Pixy Camera Sensor
#include <PixyUART.h>       //loads external arduino library to set up CM Pixy Camera Sensor
#include <SPI.h>           //loads external arduino library. This library is not used but required by SFE_LSM9DS0 library
#include <SFE_LSM9DS0.h>   //loads an IMU library written by a sensor manufacturer and modified by me
#include "PowerRelay.h"    //loads a custom library to set up a relay to turn power on and off
#include "Voltmeter.h"     //loads a custom library to set up an analog pin to read voltage on a source battery
#include "myPID.h"         //loads an open source library to set up PID/PD control. 
#include <Servo.h>         //loads a servo library, also included inside DiggerArm, here as a reminder. HAS A BUGGED read() method as of 8/11/2014

//#include "OpticalEncoder.h"//loads a custom library to read encoders using interrupt routine 
//#include "Encoders.h"      //sets up ISR interrupt functions. Should merge optical encoders into here
//#include "Switches.h"   //methods containing ISR interrupt  functions used to keep track of which switches are pressed
#include "driveMethods.h"  //contains locomotion drive functions
#include "visionMethods.h" //contains functions setting up Pixy camera
//#include "LED.h" //loads a custom library that turns LED on and off, used for debugging purposes
#include "ChargingDetector.h" //load a file to set up charging dection 
//#include "IRsensor.h"  //load a custom library to set up IR distance sensors
//#include "DigitalProximity.h" //loads a custom library to set up a digital proximity sensor 
//#include "AntBuzzer.h" //loads a custom library to set up a speaker/buzzer for debugging purposes
#include "enableModes.h" //sets up mode changing 

#include "LinkArduinosI2c.h" //loads a header file with high level I2C communication commands to link main board and radio MCUs
#include "MasterSlaveProtocol.h" //loads custom protocol used to communicate between two boards
#include "WireReset.h" //enables arduino to self reset iself
#include "RandomGenerator.h" //generates random numbers to enable probabilistic behaviour.
#include "mpr121.h" //for capacitive sensor
#include "CapacitiveSensor.h"
#include "MAG3110.h"


#include <SPI.h> // SPI comm with SD card
#include <SD.h> // SD card library
File myFile;
#define SD_CLR_SWITCH 6  // Clear files from SD card

#define CURRENT_SAMPLE_SIZE 100 //sets a number of samples to be used for reading current averages
#define VOLTAGE_SAMPLE_SIZE 100

#include "hardSerLCD.h"
hardSerLCD lcd;


// #include <wdt.h>
// **********  END   {LIBRARY IMPORT} ---------

// ********** BEGIN {GLOBAL VARIABLE DECLARATION} **********
// --- actuator setup
// MotorBoard Drive(enable1,phase1,enable2,phase2); //sets up motor drive, calling class MotorBoard to create an object "Drive"
MotorBoard Drive; //sets up motor drive, calling class MotorBoard to create an object "Drive"
DiggerArm Arm;   //sets up arm control, calling class DiggerArm  to create an object "Arm"
// --- current sensor setup
CurrentSensor Current; //sets up a current sensor. CATION: removed constructor input
#define CURRENT_SAMPLE_SIZE 50 //sets a number of samples to be used for reading current averages
// --- gripper sensor variables
//sensor threshold is defined inside GripperSensor.h 
//GripperSensor HeadSensor; 
//sets up proximity sensors used to detect granular media //JSP
GripperSensor LUSensor(LUGripperPin);
GripperSensor LDSensor(LDGripperPin);
GripperSensor RUSensor(RUGripperPin);
GripperSensor RDSensor(RDGripperPin);
MAG3110 FSensor;

CapacitiveSensor CapSensor(CapacitiveSensorPin);
// --- IMU stuff
#define LSM9DS0_XM  0x1D // Would be 0x1E if SDO_XM is LOW
#define LSM9DS0_G   0x6B // Would be 0x6A if SDO_G is LOW
LSM9DS0 dof(MODE_I2C, LSM9DS0_G, LSM9DS0_XM); //sets up IMU (gyrsocope, magnetometer, accelerometer)


// --- camera sensor setup
/* vision stuff */
// PixyI2C pixy;       //sets up pixy camera sensors, calling class PixyI2c to create an object "pixy"
PixyUART pixy;       //sets up pixy camera sensors, calling class PixyUART to create an object "pixy"
uint16_t blocks;    //store number of blocks detected when frames are sampled
//RIGHT NOW, THERE ARE ONLY 3 VISION ITEMS
bool Object[5]; //array to hold boolean variables to tell whether or not the object of interest has been detected
uint16_t x1, xc, x7, xt, xCharging; //declare storage variables  x1=pheromone trail, xc= charging pheromone, x7 and xt are cotton stuff
uint16_t Area1, Areac, Area7, Areat, AreaCharging; //declare storage variables;

double Setpoint, Input, Output; //define vars
double KP=Kp;
double KI=KI;
double KD=KD;
myPID PD(&Input, &Output, &Setpoint, KP,KI,KD); //PID control
char lastDriveState=0; //used to keep track of Forward/Backward/Right/Left/Stop commands

// --- switches
int switchState; //used to set up contact switches
bool disableContacts = false; //flag used to mask interrupts if the robot is stuck in a routine for too long
unsigned long whenDisabledContacts=0; //timer used to remember when contact switches were disabled
unsigned long howLongWasContact=0; //timer counter used to track duration of a contact 
unsigned long whenWasLastContact=0; //record time of last contact

int current_target_heading=IN_DIRECTION; //in charging mode, keep track of desired dir
int LFC;
int RFC;
int LSBC;
int RSBC;
int LSFC;
int RSFC;
int LBC;
int RBC;
int FS;
int LS;
int RS;
int BS;

// bool sawSomeone;
bool goingIn;
bool goingOut;
bool goingCharging;
bool chargingMode;
bool diggingMode; //used to declare that the robot is in a process of digging
bool dumpingMode; //used to declare that the robot is disposing of its payload
bool restingMode;
bool exitTunnelMode;
bool turnReversalMode;
int nextMode;
bool turn_reversal_direction; //decides which direction the robot will turn in turn reversal

bool manualMode=false; //used to mask i2c Write back, i2c appears to lock up when writing back and forth
bool uselessRun=false; //used in jamming

PowerRelay Relay; //initiating an object to turn motor and camera power on and off using 1 pin
//--- voltage tap
Voltmeter Voltage;
int checkPowerCount = 0; //variable to prevent robot from going charging due to a random voltage drop 
#define CHECK_POWER_CNT_THRESH 500

// This enumeration is used in the switch-case statements in loop() to conduct any necessary tests
enum Test {
	TEST_IMU,
	TEST_IMU_CAL,
	TEST_FORCE,
	TEST_MAG,
	TEST_CAP_0, 					// remember that the thresholds might be different when the robot is plugged in. This will make it harder to debug issues associated with the capacitive sensors
	TEST_CAP_1,
	TEST_CAP_2,
	TEST_CAP_3,
	TEST_CAP_4,
	TEST_CAP_5,
	TEST_CAP_6,
	TEST_CAP_7,
	TEST_CHARGER,
	TEST_CURRENT,
	TEST_HALL,
	TEST_SWITCHES, 			// Ross: I think this testing approach is deprecated. Use TEST_CAP instead
	TEST_DRIVE_MOTORS, 
	TEST_SERVO_MOTORS, 
	TEST_CAMERA,
	TEST_VOLTAGE,
	TEST_GRIPPER_SENSOR,
	TEST_POWER_SENSORS, 
	TEST_TURN_HEADING,
	TEST_PICK_DIRECTION,
	TEST_PID_CONTROLLER,
	TEST_NOTHING,
};


//--- set up IR distance sensors
//IRsensor IRright(IRsensorRightPin);
//IRsensor IRleft(IRsensorLeftPin);
//DigitalProximity FrontBumpSensor(ProximityBumpPin);
// ********** END   {GLOBAL VARIABLE DECLARATION} ----------

// bool watchdogFlag=1; //is set high when action is performed and pulled low when code cycles. If the flag stays low for a while, robot is presumed to be stuck 
// unsigned long watchdogReset; //store time when watchdog was last reset

//quick global vars to test out some stuff

unsigned long last_dash;

unsigned long dirCheckTimer; //quick workaround to prevent instantaneous dir changing
bool dirCheckFlag;
int numOfConsequitiveBackwardKicks=0;

// bool preferGyro = false; //duct tape solution to use gyroscope to do 180 degree turns 

int StartIndicatorAddr = 0;

void printFresh(String lcddata){
    lcd.clear();
		lcd.setBrightness(30);
    lcd.print(lcddata);
    delay(500);
}

void WDT_Setup(){ // my default time is 18 seconds
	//15 seconds - resets when exiting tunnel
  	double desiredTimeout = 18;

  	double timeout2 =(int)( desiredTimeout * 227);  //227
  
  	timeout2 = 0x0fff2000 + timeout2; // 0xfff2000 is very inportant
  	WDT_Enable(WDT, timeout2);  
  	// number of loops:
	// 0x0fff2000 0
	// 0x0fff200f 231
	// 0x0fff2fff 2981
	// WDT_Restart(WDT); //USE THIS TO RESET WATCHDOG EVERYWHERE

}    

// ********** BEGIN (SETUP SCRIPT} **********

unsigned long globalTimerDiff = 0;
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
void loop(){

	Serial.println("main loop");
	
	
	// This is advantageous in that adding a new test is as simple as adding a test state to the global enumeration and adding a test method to a separate test.cpp file (does not currently exist)
	// enumeration defined in global declaration, and TEST_CASE is in RobotSelector
	switch(TEST_CASE){
		case TEST_IMU_CAL:
			TestIMUcal();
			break;
			
		case TEST_CURRENT:
		float C;
		// pinMode(currentSensorPin, INPUT);
			Serial.println(String(currentSensorPin));
			while(1){
				Serial.println("Analog reading is " + String(analogRead(currentSensorPin)));
			  C=Current.ReadAvg(CURRENT_SAMPLE_SIZE);
				Serial.println("Current reading is " + String(C));
				delay(1000);

				WDT_Restart(WDT);
				printFresh(String(C));

			
			}
			break;
			
			
		case TEST_VOLTAGE:
		float V;
		// pinMode(currentSensorPin, INPUT);
			Serial.println(String(voltage_pin));
			while(1){
			delay(3000);
				Serial.println("Analog reading is " + String(analogRead(voltage_pin)));
				V = Voltage.GrabAvg(VOLTAGE_SAMPLE_SIZE);
				Serial.println("Voltage reading is " + String(V));
				printFresh(String(V));
				delay(1000);
				WDT_Restart(WDT);
			}
			break;
			
			
			
			
		case TEST_HALL:
			TestHallEffectSensors();
			break;
			
		case TEST_IMU:
			TestIMU();
			break;
		case TEST_PID_CONTROLLER:
			// if(goingOut){
				TestPDController();
			// }
			break;
		case TEST_SWITCHES:
			TestSwitches();
			break;
		case TEST_FORCE:
				//For Force Sensitive Resistor Test and Calibration
			while(1){
				Serial.println(analogRead(ForceSensor));	
				if(CheckPayload()){
					Serial.println("Payload Detected");
				}
				delay(200);
			}
			break;
		
		case TEST_CHARGER:
			while(1){
				WDT_Restart(WDT);
			
				if(CHARGER){
					Serial.println("Charger detected");
				}
				else{
					Serial.println("Charger not detected");
				}
				
				delay(1000);
			}
			
		
		
		case TEST_MAG:
			//for magnetometer MAG3110 sensor test and calibration
			
			// Relay.PowerOff();
			// delay(1000);
			// Relay.PowerOn();
			// FSensor.setup();
			
			// delay(1000);
			
			while(1){ 
				WDT_Restart(WDT);
				FSensor.measure_values();
				delay(1000);
			}
			break;
			
		case TEST_CAMERA:
			Serial.println("Testing camera...");
			TestCamera();
			WDT_Restart(WDT);
			break;
		
		case TEST_CAP_0:
				//for capacitive sensor test and calibration
			testCap(0);
			break;
		case TEST_CAP_1:
				//for capacitive sensor test and calibration
			testCap(1);
			break;
		
		case TEST_CAP_2:
				//for capacitive sensor test and calibration
			testCap(2);
			break;
		case TEST_CAP_3:
				//for capacitive sensor test and calibration
			testCap(3);
			break;
		case TEST_CAP_4:
				//for capacitive sensor test and calibration
			testCap(4);
			break;
		case TEST_CAP_5:
				//for capacitive sensor test and calibration
			testCap(5);
			break;
		case TEST_CAP_6:
				//for capacitive sensor test and calibration
			testCap(6);
			break;
		case TEST_CAP_7:
				//for capacitive sensor test and calibration
			testCap(7);
			break;			
			
		case TEST_DRIVE_MOTORS:
			TestDriveMotors();		
			break;
		case TEST_SERVO_MOTORS:
			TestServoMotors();
			break;
		case TEST_GRIPPER_SENSOR:
			// Serial.println(analogRead(FGripperPin)); // FGripperPin not defined
			TestGripperSensor();
			// WDT_Restart(WDT);
			break;			
		case TEST_POWER_SENSORS:
			TestPowerSensors();
			break;
		case TEST_TURN_HEADING:
			TestTurnHeading();
			break;
		case TEST_PICK_DIRECTION:
			TestPickDirection();
			break;
		case TEST_NOTHING:
			// Serial.println("Test intentionally ignored");
			break;	
		default:
			// Serial.println("Default test case. TEST_CASE not properly assigned?");
			break;
	}
// int loopNum = 0;
 // Daniel debug
		while(1){     
      
//    Forward(BASE_SPEED);
//    TestPower();
//    delay(4000);
//    Stop();
//    TestPower();
//    delay(1000);
//    Backward(BASE_SPEED);
//    TestPower();
//    delay(7500);
//    Stop();
//    TestPower();
//    delay(1000);

    Right(RIGHT_BASE_SPEED);
//    TestPower();
//    delay(3750);
//    TestPower();
//    delay(3750);
//    Stop();
//    TestPower();
//    delay(2000);
//    Left(LEFT_BASE_SPEED);
//    TestPower();
//    delay(3750);
//    TestPower();
//    delay(3750);
//    Stop();
//    TestPower();
//    delay(2000);

//// turn right
//    Forward(200);
//    delay(500);
//    Drive.RightForward(50);
//    Drive.LeftForward(200);
//    delay(2500);
//    Stop();
//    delay(1000);
//    Backward(200);
//    delay(500);
//    Drive.RightBackward(200);
//    Drive.LeftBackward(50);
//    delay(2500);
//    Stop();
//    loopNum= loopNum+1;
//    printFresh("loopNum =" + String(loopNum));
//    delay(1000);

		}
   
	if(goingIn){
		PD.SetTunings(Kp, Ki, Kd); // Ross' version of resetting the gains -- I don't think this is necessary
		current_target_heading = IN_DIRECTION;
		GoingInMode();
	}

	if(diggingMode){
		Serial.println("diggingMode");
		while(diggingMode){
			DiggingMode();
			//Serial.println("Digging Mode"); // JSP //bani commented
		}
	}

	if(dumpingMode){
		Serial.println("dumpingmode");
		current_target_heading=OUT_DIRECTION;
		while(dumpingMode){
			DumpingMode();
			//Serial.println("Dumping Mode"); //JSP //bani commented
		}
	}

	if(goingOut){
		PD.SetTunings(Kp, Ki, Kd); // Ross' version of resetting the gains -- I don't think this is necessary
		current_target_heading = OUT_DIRECTION;
		goingOutModeRoss();

	}

	if(goingCharging){
		GoingCharging();
	}
 
	if(chargingMode){
		ChargingMode();
	}
 
	if(restingMode){
		KP=Kp; //reset gain
		RestingMode();
	}
 
	if (exitTunnelMode){
		exitTunnel();
	}
 
	if (turnReversalMode){
		TurnHeadingRoss(current_target_heading);
	}

}//end main loop
// ********** END   {MAIN SCRIPT} ----------

// ********** BEGIN (MODE DEFINITION} **********



//----------------------------------------------------
void goingOutModeRoss(){
	Serial.println(F("Beginning of GoingInMode()"));
	writeSDcard('M', "Going Out", millis());

	WDT_Restart(WDT);
	numOfConsequitiveBackwardKicks = 0;

	#ifdef FIO_LINK
		Serial.println(F("FIO_LINK defined"));
		printFresh("Going out"); //report over radio 
	#endif

	// #if ALLOW_USELESS_RUNS
		// unsigned long whenModeStart=millis(); //the robot has X seconds to get to the tunnel or it has to get out
	// #endif

	// unsigned long whenMovedHead=millis();  //initiate timer to myDelay head shaking; //pitch head up and down to make sure that the head sensor triggers if the robot is pushing in a tunnel

	Arm.PitchGo(HIGH_ROW_ANGLE);
	Arm.GripperGo(CLOSED_POS); //close the jaws //JSP

	// TurnHeading(current_target_heading); //may need to add this for a case when the board resets
	// add head bump sensor
	Serial.println(F("goingOutModeRoss is..."));
	
	
	while(goingOut){
		// Serial.println("In goingIn while-loop");
		// Serial.print("The goingIn cycle-time is: ");
		// Serial.println(millis() - previousTime);
		// previousTime = millis();
		
		
		if(millis() - globalTimerDiff > 2000){
			sendPowerUsage();
			globalTimerDiff = millis();
		}
		
					//--- handle wrong way directions
		Forward(BASE_SPEED); // Drive forward for the duration of the heading-check statement
		if(!isWantedHeading(OUT_DIRECTION)){
			Serial.println("Not facing the correct direction");
			Stop();
			enable_turnReversalMode(3);
			current_target_heading=OUT_DIRECTION;
			TurnHeadingRoss(OUT_DIRECTION);
			//whenForcedBackwardKick=millis(); //reset timer to prevent immediate backup
			
				#ifdef FIO_LINK
					Serial.println(F("FIO_LINK defined"));
					printFresh("Going out"); //report over radio 
				#endif
		}	
		FollowLane(); //poll camera and call PD

		WDT_Restart(WDT);
		// Arm.PitchGo(HIGH_ROW_ANGLE);
		// Arm.GripperGo(CLOSED_POS); //JSP
		 
		// Checks for Contact -- will be calling followLane() within the contact check loop
		if(CONTACT){
			WDT_Restart(WDT);
			handleContact();
			
			// Rewrite fio to goinging state so we know we are out of the turning state
			#ifdef FIO_LINK
				Serial.println(F("FIO_LINK defined"));
				printFresh("Going out"); //report over radio 
			#endif
				writeSDcard('M', "Going Out", millis());

		}
		
		// If we run into the media - copied from front contact
		if(checkHeadSensor()){
			Backward(BASE_SPEED);
			delay(500);
			Drive.RightForward(255);
			Drive.LeftForward(75);
			delay(500);
			Drive.RightForward(75);
			Drive.LeftForward(255);
			delay(500);
		}
		
	
 
		Forward(BASE_SPEED); // Drive forward for the duration of the heading-check statement
		if(CHARGER){
			Stop();
			enable_DumpingMode();
			return;
		}
		FollowLane();//poll camera and call PD
		WDT_Restart(WDT);
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

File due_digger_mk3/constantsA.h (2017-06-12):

// ********** BEGIN {MISC TUNABLE CONSTNATS} ----------
#define GO_DIG_PROB   50  
#define GO_REST_PROB  50 //not used in a code, included for amusement purposes.

// #define DUMPING_TARGET_THRESH 5000 //minimum area of a dumping target to be detected  //10K works up close with the beacon turned sideways
#define CHARGING_GROUND_TRAP 100 //minimum area the robot must see
#define CHARGING_TARGET_THRESH 1000 //minimum area to start driving to a docking station
#define CHARGING_DOCKING_THRESH 20000 //area needs to be seen to initate docking  //unused i think
#define LOWEST_ALLOWABLE_VOLTAGE 3.4//5v Power is lost when battery level reaches 3v, step up chip no longer functions  //3.3 too low
#define CHARGED_VOLTAGE 3.8 // 3.65 appears to be the max voltage  //3.79 was too high

// #define TURNING_THRESH 1000 //minimum area needed to terminate feedback turning  //modified

////////////////////////////////////////////// Pitch Servo Parameters //////////////////////////////////////////////
#define LOW_ROW_ANGLE   60 //45, JSP  //pitch servo is commanded to point toward ground
#define HIGH_ROW_ANGLE  120 //120 //100, JSP //pitch servo is commanded to point toward the ceiling without blocking camera 
#define MID_ROW_ANGLE   60//85, JSP//pitch servo is commanded to be parallel to ground
#define TRAVEL_ANGLE    60//90, JSP     //pitch servo will be maintained around this setpoint while the robot is driving 

////////////////////////////////////////////// Gripper Servo Parameters //////////////////////////////////////////////
#define CLOSED_POS 80 //85//110//179, JSP  //grip servo fully closed angle
#define OPEN_POS 55//90, JSP     //grip servo fully open angle
#define MID_POS 70 //JSP //grip servo half-open angle

#define ForceSensorThresh 100 // JSP

////////////////////////////////////////////// Capacitive Sensor Parameters //////////////////////////////////////////////
// #define AntThresh 3 // Ant Detection Threshold for Capacitive Sensor

#define WallSingleThresh1	500 //Wall Detection, Single Contact Threshold for Capacitive Sensor - Lower
#define WallSingleThresh2 650 //Wall Detection, Single Contact Threshold for Capacitive Sensor - Upper

#define AntSingleThresh1	50
#define AntSingleThresh2	500

#define WallDoubleThresh1 10000 //1 //for Wall Detection, two or more contact threshold for Capacitive Sensor
#define WallDoubleThresh2 100000 

#define AntDoubleThresh1 1	//for Ant Detection, two or more contact threshold for Capacitive Sensor - Lower
#define AntDoubleThresh2 50 // Upper

////////////////////////////////////////////// PixyCam Parameters //////////////////////////////////////////////
#define MINIMUM_AREA_THRESH 20   //ensure that only blocks that are at least this big are considered. Also can be configured in camera via PIXYMON

////////////////////////////////////////////// IMU Direction Parameters //////////////////////////////////////////////
#define OUT_DIRECTION 263 //240//291//300 // previously set to 270-  //modified // Ross10/11 changed 270->291 
#define IN_DIRECTION  90 //89//30 //  used to be 60  //modified
#define GET_BACK_DIRECTION 25 //compass direction
#define CHARGING_DIRECTION 240//240//300 //170 is at the wall, towards me
#define DIRECTION_UNCERTAINTY 60 //used to be 5. increased to 10
#define PORT_DIRECTION        357 //11//11//355//350    //left with respect to IN_DIRECTION  //modified
#define STARBOARD_DIRECTION   17 //150//167   //right with respect to IN_DIRECTION  //modified Ross10/11 changed 170->200

////////////////////////////////////////////// IMU Bias Parameters //////////////////////////////////////////////
#define HX_MIN -0.2100
#define HX_MAX 0.0700

#define HY_MIN -0.1000
#define HY_MAX 0.2000

#define PHD 0 // Positive Heading Direction: 0 for CW and 1 for CCW
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

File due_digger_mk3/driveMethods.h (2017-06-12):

/* this file contains drive methods and functions */

#include "Arduino.h"
#include "RobotSelector.h"
// #include "MasterSlaveProtocol.h"
// #include "DigitalProximity.h" //possibly a bug. compiler cant find extern DigitalProximity
// #include "IRsensor.h" //possibly a bug. compiler cant find extern IRsensor
//---used by Forward, Backward, Right, Left, Stop
extern char lastDriveState;
extern MotorBoard Drive;
extern uint16_t x1, xc, x7, xt; //declare storage variables
//---used by DriveForward
extern double Setpoint, Input, Output; //define vars
extern myPID PD;
extern uint16_t Area1, Areac, Area7, Areat; //declare storage variables;
extern bool goingIn;
//used by ...
extern void GetDetectedSigs();
extern bool Object[]; //various objects. MAY NEED TO SPECIFY INDIVIDUALLY
// extern bool Object[6]; //COTTON
//---used by FollowLane
extern void myDelay(unsigned long);
extern void TurnHeading(float);
// extern unsigned long last_dash; //keep track of last robot dash forward if trail is missing
//---used by pick_going_charging_direction
// extern uint16_t DUMPING_TARGET_THRESH;
//---used by go_docking
// extern void bumpDelay(unsigned long delayTime);
extern bool isChargerDetected();
// extern void handleContact();
// extern bool handleIRcontacts();
// extern void enable_ChargingMode();
// extern void enable_GoingInMode();
// extern void enable_RestingMode();
// extern void enable_GoingCharging();
// extern bool CheckPower();
// extern GripperSensor HeadSensor;
// extern  DigitalProximity FrontBumpSensor;
// extern IRsensor IRright;
// extern IRsensor IRleft;
// extern GripperSensor HeadSensor;
//---used by redock
extern PowerRelay Relay;  
//---used by get_back_on_trail
// extern int current_target_heading;


//----------------------------------------------------

void Forward(int speed){
  Drive.RightForward(speed);
  Drive.LeftForward(speed);
//  Serial.println("Forward");
  // lastDriveState=drivingForward;

}
//----------------------------------------------------
void Backward(int speed){  
  Drive.RightBackward(speed);
  Drive.LeftBackward(speed);
//  Serial.println("Backward");
  // lastDriveState=drivingBackward;
}
//----------------------------------------------------
void Right(int speed){
  Drive.RightBackward(speed);
  Drive.LeftForward(speed);
//  Serial.println("Right");
  // lastDriveState=turningRight;
}
//----------------------------------------------------
void Left(int speed){
  Drive.RightForward(speed);
  Drive.LeftBackward(speed);
//  Serial.println("Left");
  // lastDriveState=turningLeft;
}
//----------------------------------------------------
void Stop(){
  Drive.RightStop();
  Drive.LeftStop();
 // lastDriveState=stopped;
}

//----------------------------------------------------
void DriveForward(uint16_t x){
	/* this method implements PID controller to drive forward
	input is a pixy block x coordinate 
	pwmR=+ output
	pwmL=- output
	*/
	Input=x;
	//Setpoint=160; // 320/2=160, center pixel
	PD.Compute(); //updates controller
	//command right wheel
	#if defined(ROBOT_A) || defined(ROBOT_B) || defined (ROBOT_C)
		int pwmR=BASE_SPEED + (int)Output;
	#endif

	#ifdef ROBOT_D
		int pwmR=BASE_SPEED + (int)Output; //JSP
		//int pwmR=BASE_SPEED - (int)Output; //Vadim's code
	#endif

	#ifdef ROBOT_E //JSP
		int pwmR=BASE_SPEED + (int)Output; // JSP
	#endif // JSP

	if (pwmR>255){ 
		pwmR=255; //guard against overflow 
	} 
	if (pwmR < 0 ){ //differential turning is needed
		pwmR=0;
 // pwmR=-1*pwmR; //flip the sign
  // if(pwmR>255){ 
  // pwmR=255; //guard against overflow
  // } 
 // Drive.RightBackward(pwmR);
	}
 // else{
	Drive.RightForward(pwmR);
 // }

	//command left wheel
	#if defined(ROBOT_A) || defined(ROBOT_B) || defined (ROBOT_C)
		int pwmL=BASE_SPEED - (int)Output; //Note the sign of PV is different comparing to the statement above
	#endif
	
	#ifdef ROBOT_D
		int pwmL=BASE_SPEED - (int)Output; //JSP
		//int pwmL=BASE_SPEED + (int)Output; //Note the sign of PV is different comparing to the statement above
	#endif

	#ifdef ROBOT_E
		int pwmL=BASE_SPEED - (int)Output; //JSP
	#endif

	if (pwmL>255){ 
		pwmL=255;
	} //guard against overflow
	
	if (pwmL < 0 ){ //differential turning is needed
		pwmL=0;
		// pwmL=-1*pwmL; //flip the sign
		// if(pwmL>255){ 
		// pwmL=255;
		// } //guard against overflow
	// Drive.LeftBackward(pwmL);
	}
	// else{
	Drive.LeftForward(pwmL);
	// }
	Serial.print(pwmR); 
	Serial.print('\t');
	Serial.println(pwmL);
}

// ----------------------------------------------------
void DriveBackward(uint16_t x){
	/* this method implements PID controller to drive forward
	input is a pixy block x coordinate  */
	Input=x;
	//Setpoint=160; // 320/2=160, center pixel
	PD.Compute(); //updates controller
	//command right wheel
	int pwmR=BASE_SPEED - (int)Output; // used to be +
	if (pwmR>255){ 
		pwmR=255; //guard against overflow 
	} 
	
	if (pwmR < 0 ){  //guard against overflow
		pwmR=0;
	} 
	Drive.RightBackward(pwmR);
 

	//command left wheel
	int pwmL = BASE_SPEED + (int)Output; // used to be -
	if (pwmL>255){ 
		pwmL=255; //guard against overflow 
	} 
	if (pwmL < 0 ){  //guard against overflow
		pwmL=0;
	} 
	Drive.LeftBackward(pwmL); 
	// Serial.print(pwmR); Serial.print('\t'); Serial.println(pwmL);
}



//----------------------------------------------------
void FollowLane(){
	// Serial.println("In FollowLane()...");

	WDT_Restart(WDT);
	/* this method will make the robot to follow a pheromone trail, calls PID controller method
	DriveForward(int x). 
	Every so often the robot does a dash/kick forward to help it travel faster and 
	go over obstacles (loose GM) better */
	// Serial.println("your pixy camera is not working");
	GetDetectedSigs(); //poll camera
	// Serial.println(" ;-) "); //VADIM
	if(goingIn){
		// if(COTTON){ // area7 is associated with the area of cotton seen
			if(Area7>200){ //150
				DriveForward(x7);
				 Serial.print('cotton');
				 Serial.print("\t");
				 Serial.println(x7);
				return;
			// }
		}
	}

	// if(TRAIL1){
		if(Area1>150){
			Serial.println("Driving forward");
			DriveForward(x1);
		// }
		
		if(Area1<150){
			Serial.println("Cannot find pheromone trail");
		}
		return;
	}
 // else{ //got rid of this portion of the code, could be giving us current spikes
  // if( (millis()-last_dash) > 1500){
  // Forward(255); delay(100); //dash
  // // Forward(BASE_SPEED); //return to base speed forward
  // Forward(BASE_SPEED); //return to base speed forward
  // last_dash=millis();
  // }
 // }
}
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

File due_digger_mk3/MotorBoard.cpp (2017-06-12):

#include "Arduino.h"   //includes standard Arduino Library
#include "MotorBoard.h" //includes header file
#include "RobotSelector.h" //load appropriate robot specific definitions and constants 

// MotorBoard :: MotorBoard(int enable1, int phase1, int enable2, int phase2){
MotorBoard :: MotorBoard(){
// _phase1=phase1; _phase2=phase2; _enable1=enable1; _enable2=enable2; // storing passed values to private variables for robustness
	pinMode(phase1, OUTPUT);
	pinMode(phase2, OUTPUT);
  pinMode(phase3, OUTPUT);
  pinMode(phase4, OUTPUT);
	pinMode(enable1, OUTPUT);
	pinMode(enable2, OUTPUT);
  pinMode(enable3, OUTPUT);
  pinMode(enable4, OUTPUT);
}

void MotorBoard :: RightFrontForward(int pwm){
//	Serial.println("In RightFrontForward");
  digitalWrite(enable4,LOW);
  analogWrite(phase4,pwm);  
}

void MotorBoard :: LeftFrontForward(int pwm){
//  Serial.println("In LeftFrontForward");
  digitalWrite(enable2,LOW);
  analogWrite(phase2,pwm);  
}

void MotorBoard :: RightBackForward(int pwm){
//  Serial.println("In RightBackForward");
  digitalWrite(enable3,LOW);
  analogWrite(phase3,pwm);  
}

void MotorBoard :: LeftBackForward(int pwm){
//  Serial.println("In LeftBackForward");
  digitalWrite(enable1,LOW);
  analogWrite(phase1,pwm);
}

void MotorBoard :: RightFrontBackward(int pwm){
//  Serial.println("In RightFrontBackward");
  digitalWrite(enable4,HIGH);
  analogWrite(phase4,255-pwm);//note 255-pwm inversion! Nevermind. changed back to pwm  
}

void MotorBoard :: LeftFrontBackward(int pwm){
//  Serial.println("In LeftFrontBackward");
  digitalWrite(enable2,HIGH);
  analogWrite(phase2,255-pwm);  
}

void MotorBoard :: RightBackBackward(int pwm){
//  Serial.println("In RightBackBackward");
  digitalWrite(enable3,HIGH); //must change
  analogWrite(phase3, 255-pwm);  
}
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

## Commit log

2016-10-13 fixing a line error?
    [CapacitiveSensor.cpp]
2016-10-14 Syntax and testing
    I made the testing methods for the capacitors a little bit easier to
    execute in the fio_wireless method, and tidied up a lot of stuff as I
    read through the code.
2016-10-17 Modified testing approach
    Now adding a new test is as simple as adding a test state to the global
    enumeration and adding a test method to the switch-case implementation.
    Can capture the flow-control with an infinite loop for simply print a
    statement to Serial.
2016-10-17 TEST_DRIVE_MOTORS
    Testing that the motors on the robots which do not move have operational
    motors. They do, so there must be something off with their controller,
    or the control flow of goingInMode. Perhaps in FollowLane (meaning they
    have a bad pixy or PD parameters)
2016-10-19 TurnHeadingRoss
    Created a new TurnHeading method to start from scratch and just get the
    simplest functionality. Works well, as long as the magnetometer is
    working. If the robot starts spinning, try resetting it. This is a
    hardware issue I think I found a solution for, but Bahni would be a
    better judge of that.
    [due_digger_mk2.ino, fio_wireless.ino]
2016-10-21 Cleaning up code as I review it.
    Trying to find possibe errors in control flow for turnheading
    [driveMethods.h, due_digger_mk2.ino]
2016-10-21 More IMU testing
    I have found that I can intentionally hang the IMU, but I have not found
    a way to unhang it when it is not connected to USB
2016-10-25 I think the real problem is the connection from the IMU to the circuitry
    Add extensions and retest tomorrow. Things are looking better!
    [due_digger_mk2.ino]
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2016-10-31 Found bug in checkHeadSensor()
    [driveMethods.h, due_digger_mk2.ino]
2016-11-11 Mostly modifications I made while testing the power board issue. Still not resolved, but not as major of an issue for now.
    [constantsB.h, constantsE.h, due_digger_mk2.ino]
2016-11-30 Adding doc
    [roboticAntStatus.xlsx]
2016-12-01 December 1 Update
    Added some caster documentation
    Commented out unnecessary debugging prints
    Tuned IMU parameters
    [roboticAntStatus.xlsx]
2016-12-02 Some doc stuff mostly
    [roboticAntStatus.xlsx]
2016-12-02 December 2 Update
    [roboticAntStatus.xlsx]
2016-12-06 Fixing some capacitive sensor stuff
    [roboticAntStatus.xlsx]
2016-12-12 Capacitive sensor tuning
    [roboticAntStatus.xlsx]
2016-12-14 capacitive sensor updates
    [roboticAntStatus.xlsx]
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2016-12-21 More tuning stuff. Close to running things?
    [roboticAntStatus.xlsx]
2016-12-21 imu tuning
    [roboticAntStatus.xlsx]
2016-12-21 lots of imu tuning stuff
    [bravoIMU.csv, bravoIMU2.csv]
2017-01-02 tuned all robots
    [alphaIMU.csv, bravoIMU.csv, bravoIMU2.csv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]
2017-01-03 Formatting stuff relevant to lorenz runs and some documentation stuff
    [roboticAntStatus.xlsx]
2017-01-05 MATLAB code buff, Doc update, Parameter update
    Added a uselessRun parameter to control dumping behavior in the case of
    a useless run.
    Also commented out a lot of unused functions. Consider deleting them...
    Moved Lorenz code to the if(goingIn)-statement in the main loop, but I
    want to talk with Will before I commit to this change - pretty confident
    this is the way to go.
    Removed checkPayload from goingOutModeRoss
    Totally reworked the way that directions are checked in goingIn and
    goingOut methods
    Removed dumping_switch stuff
    [constantsA.h, constantsC.h, constantsD.h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]
2017-01-05 Revert "test"
    This reverts commit 41127ea1b7ae32a671fcc228c774af34a5d35e2f.
    [constantsA.h, constantsC.h, constantsD.h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]
2017-01-07 More PID control stuff
    Also added some camera stuff back in for detecting the color green
    [roboticAntStatus.xlsx]
2017-01-08 Updated goingOut implementation and tuned caps
    [roboticAntStatus.xlsx]
2017-01-16 01/16 Week updates
    moved lorenz/reversal stuff to robot selector so all trial stuff can be
    set from the RobotSelector.h file,
    Added a Charger testing method.
    Wrote a determineState method to allwo the robots to find where they
    were in the digging state machine prior to being turned on/reset.
    Changed the minimum threshold needed for the MAG3110 sensor. Probably
    need to tune this a bit more.
    Added some stuff to wakepUp() which re-initializes the charging
    detector. This resolved the reset on charger issue.
    Got rid of the checkStart stuff in the fio code.
    Added some followlane stuff to the visionmethods which allows the PID to
    be called mroe frequently.
    [bravoIMU.csv, charlieIMU.csv, echoIMU.csv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]
2017-01-18 01/17 commit
    [deltaIMU.csv, roboticAntStatus.xlsx]
2017-01-31 Fio no longer resets
    [CapacitiveSensor.cpp, due_digger_mk2.ino, fio_wireless.ino]
2017-02-06 Lots of updates
    I think it may be possible to remove the Fio from the robots altogether,
    but in order to do this I need to demonstrate that the Due can perform
    all of the tasks on the available pins.
    I wrote the hardSerLCD library, so that the Due can now write to the LCD
    screen on any of the open TX lines.
    I also included the .pptx Vadim wrote for starting the robots in the
    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
    [roboticAntStatus.xlsx]
2017-02-17 Transitioning away from the Fio
    [alphaIMU.csv, roboticAntStatus.xlsx]
2017-03-21 New robot prototyping
    [alphaIMU.csv, roboticAntStatus.xlsx]
2017-05-26 made to grab particles and drop them off
    Moves forward with gripper down, picks up material, raises gripper, backs out, drops off the particles, moves forward a bit, drops gripper, then repeats
2017-05-27 Control all 4 motors individually
    adjusted code to allow for all 4 motors to be controlled
2017-05-27 Added suppporting library code to the quad folder
    Intention is to implement PID control using the Pixycam
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2017-06-01 Lots of changes
    Reorganized the codebase. Deprecated files from Mk2 are now in the
    deprecated directory. New codebase is all together in due_digger_mk3
    with all of the supporting code that is needed. Note that it currently
    does not compile: still need to track down the relay and charger issues.
    I think that it is just a pin assignment issue in either the def*.h or
    the constants*.h files for A, but I could be wrong.
    [CapacitiveSensor.cpp, CurrentSensor.cpp, DiggerArm.cpp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]
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2017-06-07 Updating calibration files
    [alphaIMU.csv, bravoIMU.csv, charlieIMU.csv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]
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2017-06-07 Debugging behaviors
    [roboticAntStatus.xlsx]
2017-06-07 Solved motor communication issues
    [MotorBoard.cpp, defA.h, driveMethods.h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]
2017-06-07 try again?
    [roboticAntStatus.xlsx]
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2017-06-10 test power method included and lcd fixed
    [constantsA.h, due_digger_mk3.ino]
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2017-06-18 Just some docs
    [encoderwheel.xls]
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2017-06-26 fixed some calls in the code
    still needs some work on the constants in the PID control
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2017-06-27 Plotted all collected data from encoder
    Run plot_PID_motor_encoder to obtain plots of all the data.
    [ramp_test_1.xls, ramp_test_2.xls, ramp_test_3.xls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]
2017-07-02 4 motors encoder data and program
    [4_motor_ramp_test_1.csv, 4_motor_ramp_test_2.csv, 4_motor_ramp_test_3.csv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]
2017-07-04 fix for changing motor speeds
    pretty sure this is a solution for changing motor speeds without dropping in set position
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2017-07-06 Tests and plots of those tests
    ran a few tests where the slope of the ramp changed with respect to time and another set of tests where it changed with position. Also ran tests with different gains and plotted those to tune the val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
    [change_by_pos_ramp_test_1.csv, change_by_pos_ramp_test_2.csv, change_by_pos_ramp_test_3.csv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]
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2017-07-08 docs and testing
    [roboticAntStatus.xlsx]
2017-07-09 Worked integral control in PID
    The encoder code has been made much more accurate with integral control. The constants can be fiddled with to make it even more accurate. The script "quick_plot_2" shows the final tests and "for_the_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
    [motorB_test_1.csv, motorB_test_10.csv, motorB_test_11.csv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]
2017-07-12 work on mk2
    [Eagle.sch, roboticAntStatus.xlsx]
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2017-07-19 rearranged the files
    [4_motor_ramp_test_1.csv, 4_motor_ramp_test_2.csv, 4_motor_ramp_test_3.csv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]
2017-07-19 ross' stuff
    [roboticAntStatus.xlsx]
2017-07-20 updated the gains
    [pid_test_1.csv, pid_test_2.csv, pid_test_3.csv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]
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2017-07-22 cleg boards
    [dueSkel.brd, dueSkel.sch, dueSkelMADE.brd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]
2017-07-23 docs for bahni
    [Eagle.sch, dueSkel.brd, dueSkel.sch]
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2017-10-09 Updated codes, arduino shields, and a new repositiory
    [DRILEGEND.CFG, dueSkel2.brd, dueSkel2.sch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]

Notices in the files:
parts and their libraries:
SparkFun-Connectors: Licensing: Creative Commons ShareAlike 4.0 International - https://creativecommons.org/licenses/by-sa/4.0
